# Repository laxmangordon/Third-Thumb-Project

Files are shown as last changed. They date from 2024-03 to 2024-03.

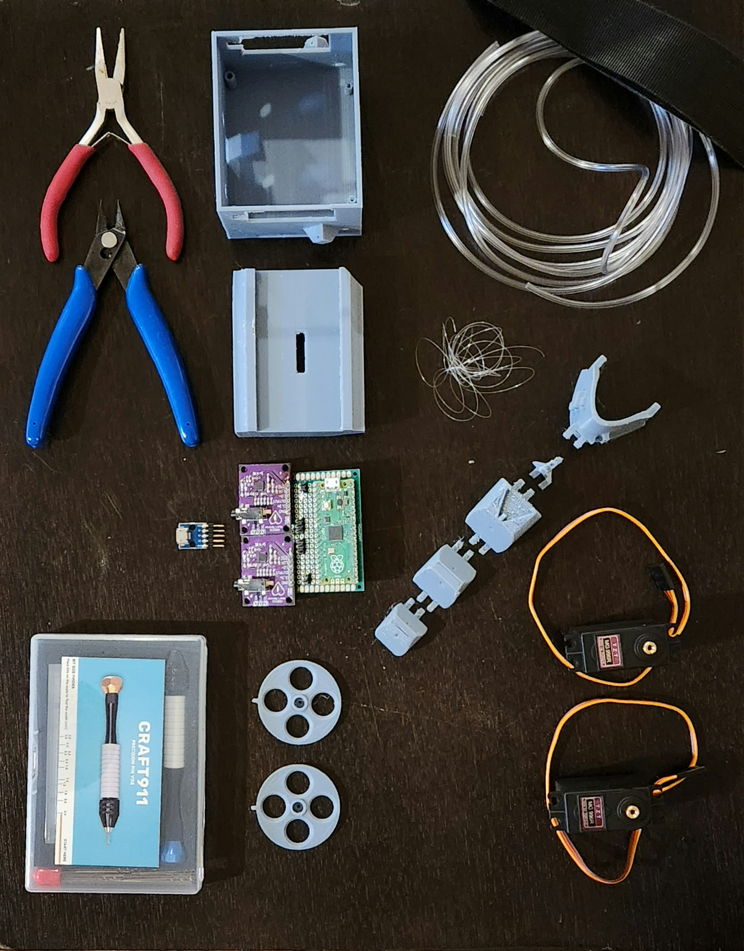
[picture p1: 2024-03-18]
projectPhotos/20240314_164508.jpg

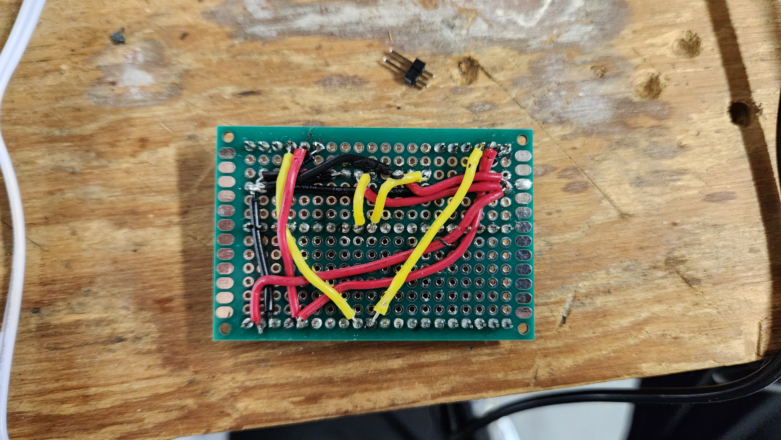
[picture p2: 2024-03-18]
projectPhotos/20240308_181342.jpg

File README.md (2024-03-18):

# Third Thumb Project
 A low cost solution to the third thumb project. Uses easilly sourced 3D printed materials, electronics modules, and everyday items such as a singular rubber band or some small tubing.

This includes all of the SolidWorks Pack and Go files in order to remix the origional creation. Also provided is are the STLs of each model incase the user does not have a licence for SolidWorks.

If you have a lisence for SolidWorks, please see the 'fingerPREVIEW.zip' file as it may help you when putting together the finger.

--------------------------------------------------------------------------------------------------------------------------

Below is the text used for the Falmouth High School Science Fair:

Background:

The inspiration for the creation of the Third Thumb came from a collaborative research project between The Plasticity Lab, University College London & Cambridge University within an article titled How Do Our Brains Adapt to Control an Extra Body Part.

The fact that the inspiration behind this project was privately owned afforded me the opportunity to create a Third thumb of similar function, but also make its design sharable to many other interested people through Open Sourcing the project.

Abstract:

This project looked to design a thumb-like appendage that can be controlled using electrical impulses from brain - nerve stimulation and is detected by electrocardiogram (ECG) feedback. The prosthetic “Third Thumb” can then be utilized by the wearer and the wearer’s neuropathways monitored as the brain “accepts” the new thumb and automatically begins to use it. The project's customized components were designed, crafted, and constructed entirely from basic and accessible materials.

What is Open Source?

Open Source is defined as projects that are made freely available for possible modification and redistribution (usually limited redistribution). Products include permission to use the source code, design documents, or content of the product. The Open Source model is a decentralized software development model that encourages the open collaboration from anyone that is willing to support the project. Some actions that one may support the project by doing are actions such as: improvement of existing features, the addition of new features, or bug fixes.

Goals:

To design a prototype prosthetic thumb from basic and accessible materials.
To create a tool for further studying the brain’s capacity to accommodate new appendages.
To afford the public domain the opportunity to adapt this model for use in projects that positively impact prosthetic / biomechanical engineering.

Special Design Considerations:

Prosthetic planes of motion - 2 axis (Abduction / Adduction, Flex / Extend) + quasi opposition rotation
Prosthetic “muscle” lines - designing appropriate leverage points for proper appendage motion using fishing line for muscles / tendons.
Wiring electrical components
Synchronizing electrical, mechanical, and bio-interfacing components.

Equipment:

3D Printer (Elegoo Neptune 2)
3D Printer Filament (PLA - Hatchbox)
Soldering Iron
Heat Gun
Isopropyl Alcohol
Precision Hand Drill
Small Wire Cutters
Pliers
WD-40
SolidWorks 2022 (CAD)
Arduino IDE 2.0

Parts:

3D Printed Case Base
3D Printed Case Mid Section
3D Printed Lid
3D Printed Servo Pulleys
3D Printed Finger Holster
3D Printed 2-axis Joint
3D Printed Finger Base
3D Printed Finger Middle
3D Printed Finger Tip
Raspberry Pi Pico
ECG Sensor (AD8232)
MG996 180° Servo
Proto-board
Breadboard Connecting Wire
Male Proto-Board Headers
Female Proto-Board Headers
22 AWG Solid Core Wire
Fishing wire
1/16" ID x 1/8" OD Clear Vinyl Tubing
Velcro Strap
1/8” Screws
5V 20,000mAh Portable Power Bank

Approximate Design and Construction Costs:

3D Printer Filament							                     $22
Isopropyl Alcohol							                       $1
WD-40									                                 $5
Raspberry Pi Pico							                       $4
x2 ECG Sensor (AD8232)				                     $8
x2 MG996 180° Servo						                      $6.50
Proto-board								                            $5
Male / Female Headers					                     $3
Fishing Wire								                           $5
25 Feet 1/16" ID x 1/8" OD Clear Vinyl Tubing		$7
Velcro Strap								                           $5
TOTAL:									                                $71.50

Impact:

This project helps to expand the availability of prosthetic technology to reach a greater audience of both prosthetic developers and non-developers. These individuals themselves can then help to further scientific fields and industry having to do with Biomechanical engineering, Medical engineering, and Robotics. With this kind of support, this could help provide a future to individuals where prosthetics that are required for the modern way of life can be purchased, upgraded, and replaced for a fraction of the price of present day variants.

Limitations:

The Raspberry Pi Pico fried itself - Lack of reverse voltage diode protecting Pi Pico voltage regulator from servos.
The unit is heavy (245 grams)
The portion of the unit that sits on the upper arm is bulky (83.5mm x 67.5mm wall to wall, and 120.5mm x 67.5mm total).
The product may not be applicable for all audience use. Factors that may prohibit the operation of this technology are impairments having to do with neuropathies or paralysis; upper extremity loss; the use of clothing or protection that obstructs the sensor to body connection or the control unit to thumb connection.
Future Design Improvements:

Decrease Weight and Size
Use slightly smaller servos
Use manufactured PCB instead of Proto-board
Use smaller microcontroller
Increase Reliability
Decrease heat generation
Separate power supply for each type of component
Use PTFE tubing instead of vinyl
Use stronger / more resilient fishing wire
EMG instead of ECG
Debug, fix, and update project motherboard

References
Clode, D. (n.d.). How do our brains adapt to control an extra body part? Dani Clode. Retrieved March 15, 2024, from https://www.daniclodedesign.com/howdoourbrainsadapttocontrolanextrabodypart
Jain, S. (2021, January 5). Introduction to Open-Source and its benefits. GeeksforGeeks. Retrieved March 15, 2024, from https://www.geeksforgeeks.org/introduction-to-open-source-and-its-benefits/
Wikipedia contributors. (2024, March 15). Open source. In Wikipedia, The Free Encyclopedia. Retrieved 13:07, March 15, 2024, from https://en.wikipedia.org/w/index.php?title=Open_source&oldid=1213835458

Special Thanks To:
Dr. Paula T. Smith
Mr. Michal Campbell
Mr. Andrew Cozzens
Mrs. Susannah Brooks
Ms. Ava K. Smith

The Third Thumb Project

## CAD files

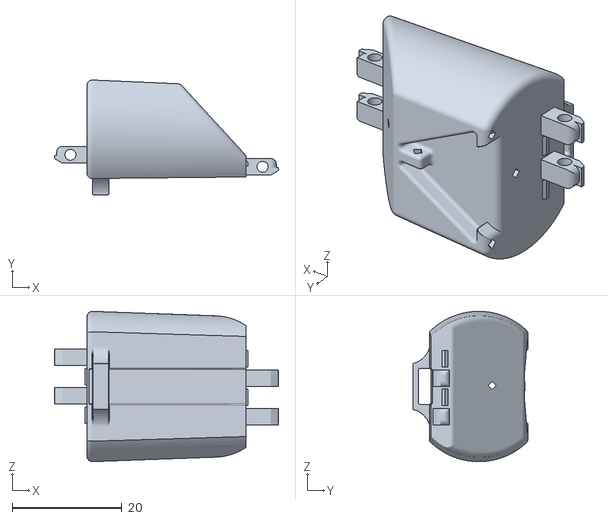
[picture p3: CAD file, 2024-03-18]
all3DModels/base/fingerBase.STL
40.8 x 20.9 x 27.4

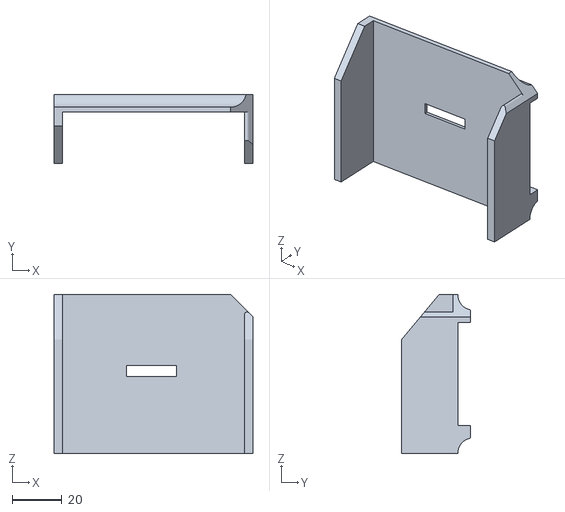
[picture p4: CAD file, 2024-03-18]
all3DModels/Case/caseMid.STL
79.8 x 27.5 x 63.8

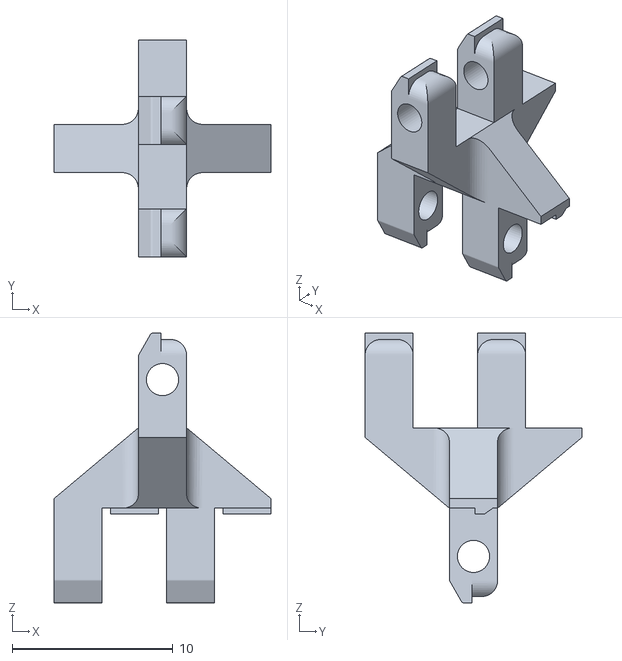
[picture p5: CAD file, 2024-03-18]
all3DModels/hinge/fingerDualAxisHinge.STL
13.5 x 13.5 x 16.8

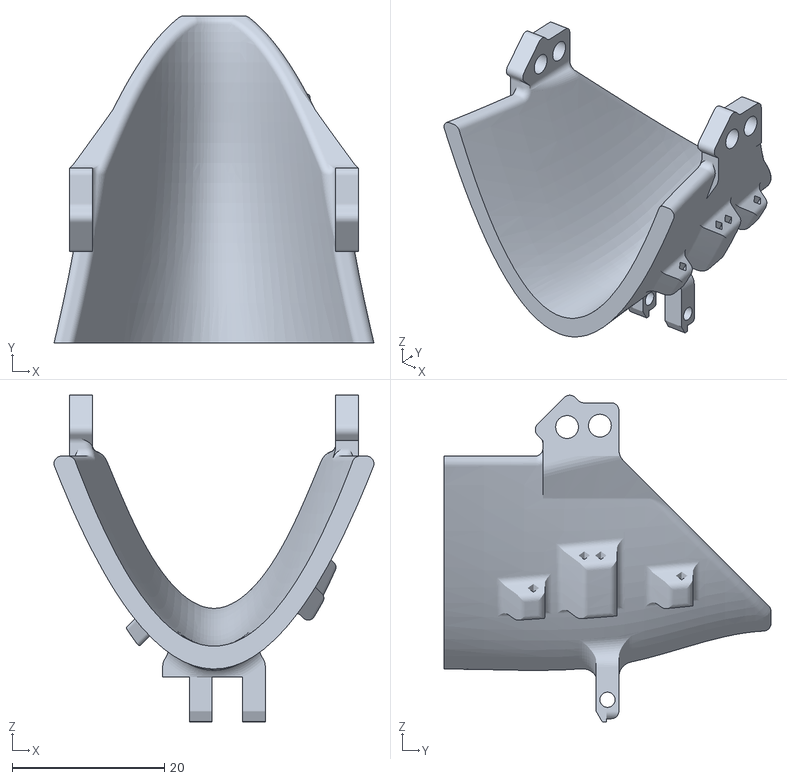
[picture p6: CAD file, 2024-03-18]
all3DModels/holster/fingerHolster.STL
42.1 x 43.0 x 42.9

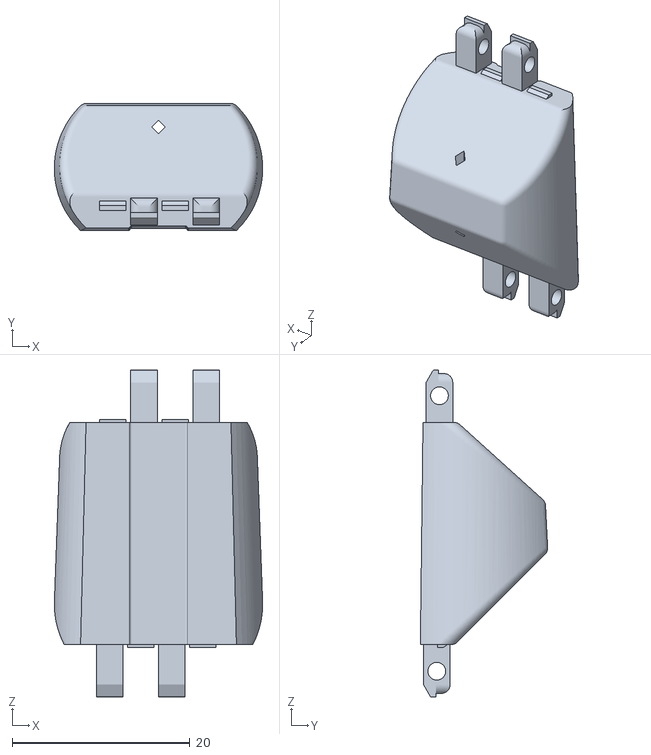
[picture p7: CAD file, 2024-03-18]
all3DModels/middle/fingerMid.STL
23.4 x 14.3 x 36.8

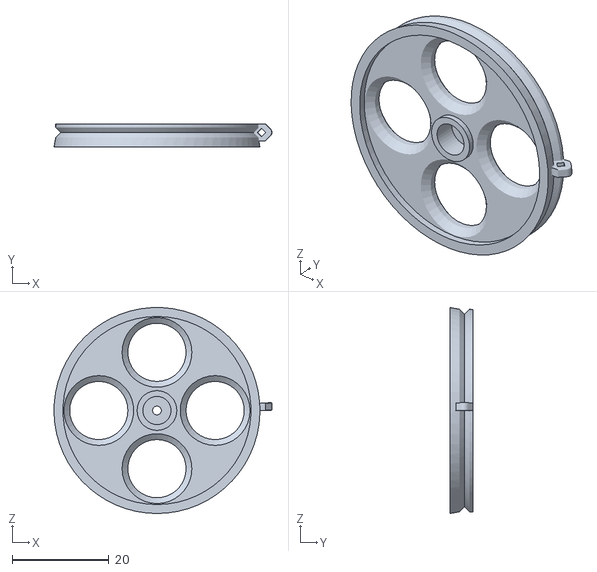
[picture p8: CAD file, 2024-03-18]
all3DModels/servoWheel/servoWheel.STL
45.0 x 4.75 x 42.5

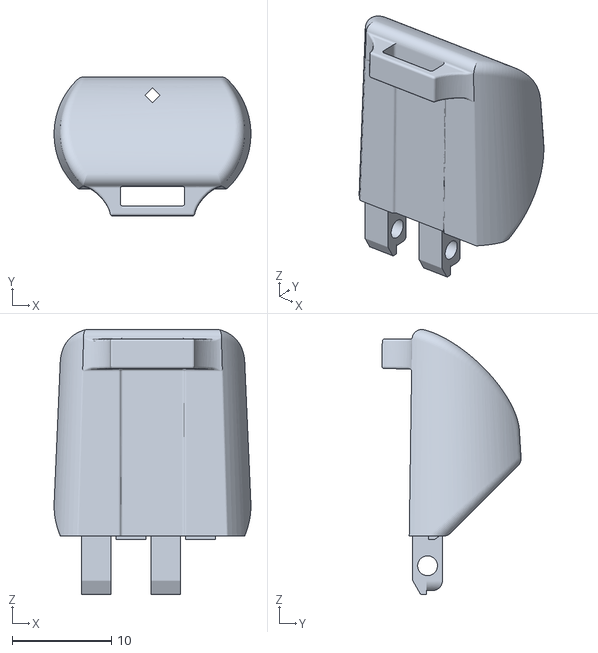
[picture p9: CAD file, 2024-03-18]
all3DModels/tip/fingerTip.STL
19.9 x 14.0 x 26.7

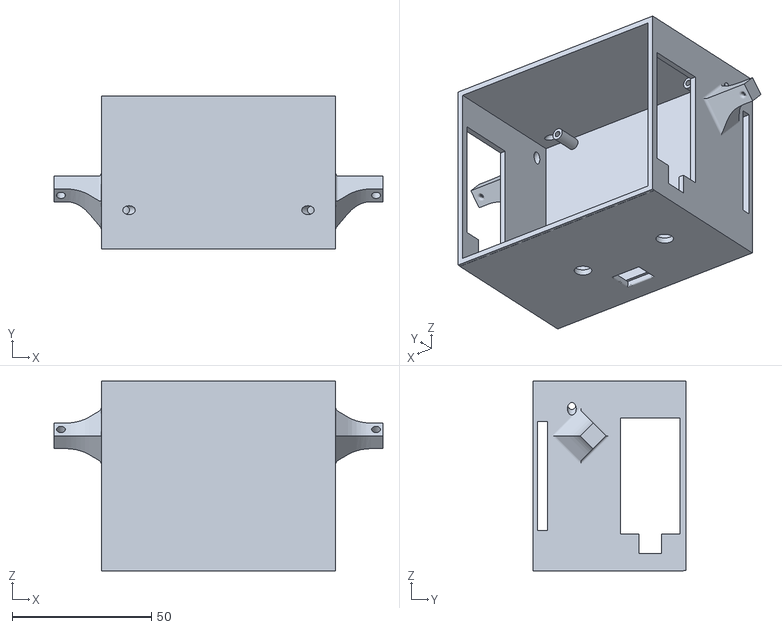
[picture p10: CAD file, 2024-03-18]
all3DModels/Case/caseBase.STL
118.0 x 55.0 x 68.0

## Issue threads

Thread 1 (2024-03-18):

Raspberry Pi Pico Voltage Regulator

laxmangordon, 2024-03-18:
When powering both of the ECG sensors and both servos together, the voltage regulator of the Pi Pico seems to get very hot and eventually break when reading data from the Pico over serial.

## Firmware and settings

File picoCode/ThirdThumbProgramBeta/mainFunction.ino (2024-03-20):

#include "mainH.h"

//define the writeServo() function
//The way that this function works is that it checks if the output of the EMG/ECG sensors have reached a threshold written below. If this is done, it will move the
//corresponding servo in one direction. This then triggers a latch and the next time the threshold is reached, the servo will move in the opposit direction. This 
//loops forever.
void writeServos(){
  //starts checking the tilt sensor and servo
  if(analogRead(tiltServoECGSensorPin) >= 700){
    while((analogRead(tiltServoECGSensorPin) >= 700) && bounceVeriable1 == false){
      if(tiltServoPos < tiltServoPosMaximum){
        setLED(1);
        tiltServo.write(tiltServoPos++);
      }
      else{
        setLED(0);
      }
      if(analogRead(tiltServoECGSensorPin) < 700){
        bounceVeriable1 = !bounceVeriable1;
      }
    }
    while((analogRead(tiltServoECGSensorPin) >= 700) && bounceVeriable1 == true){
      if(tiltServoPos > tiltServoPosMinimum){
        setLED(1);
        tiltServo.write(tiltServoPos--);
      }
      else{
        setLED(0);
      }
      if(analogRead(tiltServoECGSensorPin) < 700){
        bounceVeriable1 = !bounceVeriable1;
      }
    }
  }

  //starts checking the open and close sensor and servo
  if(analogRead(openCloseServoECGSensorPin) >= 700){
    while((analogRead(openCloseServoECGSensorPin) >= 700) && bounceVeriable2 == false){
      if(openCloseServoPos < openCloseServoPosMaximum){
        setLED(1);
        openCloseServo.write(openCloseServoPos++);
      }
      else{
        setLED(0);
      }
      if(analogRead(openCloseServoECGSensorPin) < 700){
        bounceVeriable2 = !bounceVeriable2;
      }
    }
    while((analogRead(openCloseServoECGSensorPin) >= 700) && bounceVeriable2 == true){
      if(openCloseServoPos > openCloseServoPosMinimum){
        setLED(1);
        openCloseServo.write(openCloseServoPos--);
      }
      else{
        setLED(0);
      }
      if(analogRead(openCloseServoECGSensorPin) < 700){
        bounceVeriable2 = !bounceVeriable2;
      }
    }
  }
}

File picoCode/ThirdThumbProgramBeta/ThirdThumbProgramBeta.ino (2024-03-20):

#include "mainH.h"

void setup() {

  //attaches the tilt servo to the number assigned to the tiltServoPin variable and assign the min/max pwm of the servo to 1000/2000
  tiltServo.attach(tiltServoPin, 1000, 2000);
  //attaches the open and close servo to the number assigned to the openCloseServoPin variable and assign the min/max pwm of the servo to 1000/2000
  openCloseServo.attach(openCloseServoPin, 1000, 2000);

  //Sets the pin assigned to the builtin led to the microcontroller as an output
  pinMode(LED_BUILTIN, OUTPUT);
  //sets the builtin led pin to low
  digitalWrite(LED_BUILTIN, LOW);

  //runs the startup function
  onStartup();
}

void loop() {
  //start the debugging segment of code
  debugStart();

  //start the main code functions
  writeServos();

  //start the code that resets the servos' positions
  resetServoPos();
}

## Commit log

2024-02-14 Added the 3D models for thumb
    Added the 3D models for use with a 3D printer.
    My printer:
    Elegoo Neptune 2
    Cura
    .12mm layer height
    Tree supports with .12mm distance
    [baseThumbLinkAssembly.STL, hosterLinkageAssembly.STL, middleThumbLinkAssembly.STL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]
2024-02-14 Uploaded Beta Code - NON FUNCTIONAL AS THUMB
    Beta code to test servo motors working with the raspberry pi pico.
2024-03-04 Fixed some pin changes and other modifications
    Fixed pin changes
    Fixed Servo PWM timings
    Added a button that resets servos to neutral position
    Made easier to read
    [ThirdThumbProgramBeta.ino, debugFunction.ino, extrasFunctions.ino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]
2024-03-18 Adding all working files used in project
    These are all of the latest files used for the Falmouth High School Science Fair.
    [baseThumbLinkAssembly.STL, caseBase.STL, caseMid.STL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]
2024-03-18 Added Photos/Videos
    Added some photos/videos that may be helpful to the user when building the thumb or case.
